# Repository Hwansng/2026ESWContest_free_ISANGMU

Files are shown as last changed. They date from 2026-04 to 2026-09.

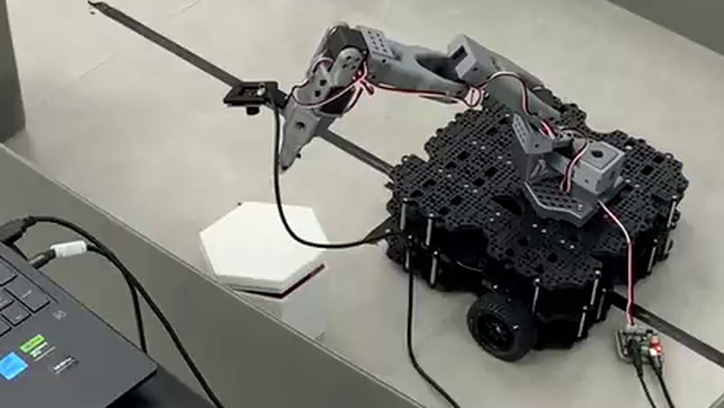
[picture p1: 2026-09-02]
report/빌드/img/grip4.png

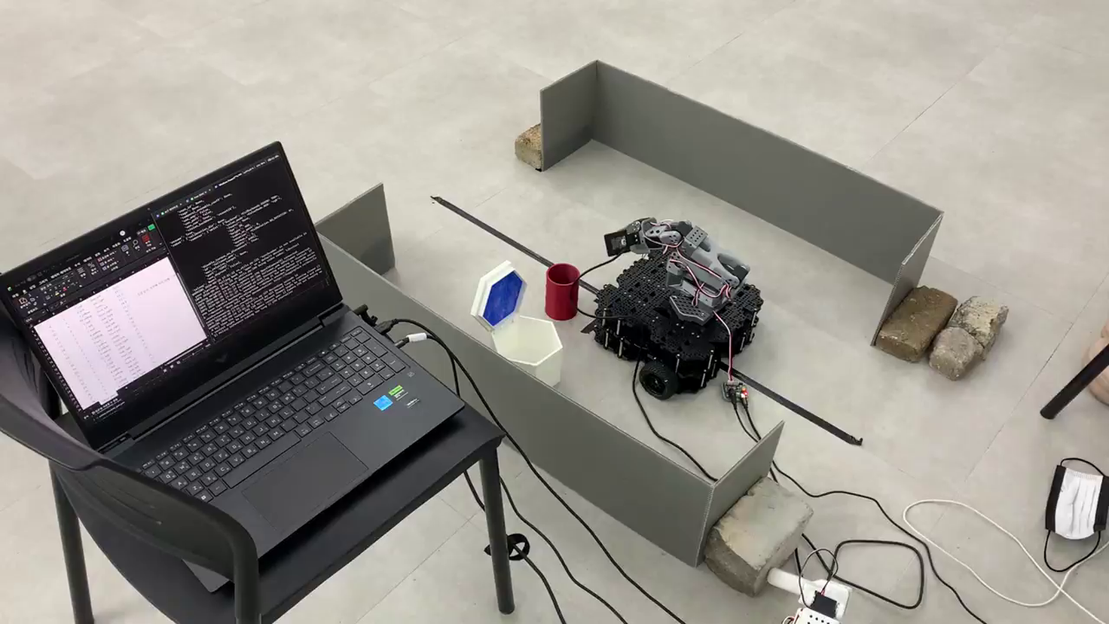
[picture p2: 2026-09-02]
report/빌드/img/rollout_wide.png

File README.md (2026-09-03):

# 🤖 HazardBot — 자율 위험물 탐지·격리 로봇 시스템

# ➕ 참가정보
 - 2026년 임베디드 소프트웨어 경진대회 (자유공모 부문)
 - 팀명: 이상무
 - 작품명: HazardBot — STS3215 직렬 버스 서보 기반 6DOF 적응형 파지 미션 기반 자율 위험물 탐지·격리 로봇 시스템
 - 팀원: 박승환, 윤강희, 이진우
 <br>

 - 주제: 듀얼 ESP32 + Raspberry Pi 5 (8GB) + ROS2 Jazzy 기반 2계층 아키텍처를 활용한 자율 위험물 탐지·격리 로봇 제작
 - 개요: 자율주행차(AMR)가 지정 영역을 자율 순찰하며, 라즈베리파이 카메라의 엣지 AI(OpenCV HSV + minAreaRect 방위각 분류)와 5종 환경 센서의 퓨전 알고리즘으로 위험물을 탐지·분류한다. 위험 등급 판별 후, UART 직렬 버스로 제어되는 6축(6DOF) Feetech STS3215 로봇 암(SO-ARM101 프레임 3D 프린팅 자체 제작)이 비대칭 물체의 방위각을 인식하고 실시간 부하(Load) 센싱 기반 컴플라이언스 토크 제어로 적응형 파지·운반 후 격리 구역의 색상별 격리함에 안전하게 배치하는 완전 자동화 미션 수행 시스템을 구현한다.
 - 개발 목표:
      - 듀얼 ESP32 기반 Fault Isolation 아키텍처 구축
      - Feetech STS3215 직렬 버스 6축 서보 데이지 체인 제어
      - 실시간 Load 센싱 기반 컴플라이언스 토크 제어 (적응형 파지)
      - OpenCV HSV + minAreaRect 방위각 분류 (60fps 엣지 비전)
      - MQ-2 가스 센서 3초 게이트 판정 (5ms × 600 표본) + 화염·거리·라인 센서 퓨전
      - ROS2 Jazzy 노드 통합 + Flask 실시간 관제 대시보드

 - 미션 시나리오:
   ```
   IDLE → PATROL → DETECTED → CLASSIFY → APPROACH → GRIP → TRANSPORT → ISOLATE → REPORT
   ```

 - 개발영상: https://youtu.be/ElTdSD-DXlM (2분 38초 · 1080p)

 ---
 # ➕ Needed (architecture)

 | `Device` | `OS` | `Middleware` | `Else` |
 | --- | --- | --- | --- |
 | Raspberry Pi 5 (8GB) | Ubuntu 24.04 LTS | ROS2 Jazzy | OpenCV 4.x, Flask + WebSocket, rosbag |
 | ESP32 DevKit V1 — **DRIVE** | Arduino-ESP32 3.0 | FreeRTOS (듀얼 코어) | TB6612FNG, VL53L1X, 5ch IR |
 | ESP32 DevKit V1 — **ENV** | Arduino-ESP32 3.0 | FreeRTOS (듀얼 코어) | MQ-2, KY-026, NeoPixel, Buzzer |
 | 학습·제어 PC (Windows 11) | — | LeRobot 0.4.4 | Feetech STS3215 × 12 (USB 반이중 어댑터), ACT |

 다음과 같은 개발환경에서 본 프로젝트를 진행한다. 모든 RPi 5 ↔ ESP32 통신은 Wi-Fi TCP 듀얼 채널이며, `<CMD,VALUE,...,CS>\n` 포맷에 **ASCII 합 % 256** 체크섬(10진수)을 사용한다.

 > **설계 변경 이력.** 초기 구상은 ESP32 한 대가 STS3215 를 UART2 로 직접 구동하는 것이었으나,
 > STS3215 는 **1선 반이중** 버스라 마스터가 하나여야 한다. ESP32 를 서보 3핀 버스에 물리면
 > 충돌이 난다. 현재는 **USB 반이중 어댑터 하나**를 마스터로 두고 PC 의 LeRobot 이 양팔을 제어한다.
 > 보드 호칭도 `#1`·`#2` 번호가 문서마다 반대를 가리켜 **DRIVE / ENV** 로 통일했다.
 > 근거와 절차는 [`docs/06_firmware/센서_지도.md`](docs/06_firmware/센서_지도.md) 와
 > [`docs/05_arm/로봇암_구축기록.md`](docs/05_arm/로봇암_구축기록.md) 참조.

 ---
 # ➕ Hardware

 | 분류 | 부품 | 용도 |
 | --- | --- | --- |
 | MCU — DRIVE | ESP32 DevKit V1 | DC 모터 · 라인트레이싱 · VL53L1X · **모터 정지 단독 권한** |
 | MCU — ENV | ESP32 DevKit V1 | 가스·화염 환경 감시 · NeoPixel · 부저 |
 | SBC | Raspberry Pi 5 (8GB) | ROS2 Jazzy + OpenCV + 대시보드 |
 | 모터 드라이버 | TB6612FNG | DC 모터 (MOSFET, 효율 95%+) |
 | DC 모터 | JGA25-371 12V | 2WD 차동 구동 (334rpm) |
 | 서보 | Feetech STS3215 × 12 | 리더·팔로워 양팔 6DOF. 1선 반이중 버스, 마스터는 USB 어댑터 하나 (12-bit, 30kg·cm) |
 | 거리 센서 | VL53L1X (ToF) | 정면 장애물 **로컬 정지 반사**(300mm · 3회 연속) · APPROACH 트리거 |
 | 가스 센서 | MQ-2 | 3초 게이트 판정 — MQ-135 는 미채택(`docs/06_firmware/센서_지도.md` §2) |
 | ~~온도 센서~~ | ~~MLX90614~~ | **미채택** — 근거는 `docs/06_firmware/센서_지도.md` |
 | 화염 센서 | KY-026 | 화염 감지 (즉시 정지) |
 | 라인 센서 | 5채널 IR 라인센서 | 라인트레이싱 PID + 이탈 감지 |
 | 프레임 | SO-ARM101 (3D 출력) | LeRobot 오픈소스 STL 자체 제작 |
 | 카메라 | RPi Camera v2 | OpenCV HSV + minAreaRect (60fps) |
 | 전원 | 3S LiPo 11.1V | **XL4016** → RPi 5 전용 · **XL4015** → 1to2 XT60 → ESP32 2보드. 실배선 정본은 [`docs/06_firmware/전력계통_실배선_2026-08-28.md`](docs/06_firmware/전력계통_실배선_2026-08-28.md) |

 ---
 # ➕ System Process

 다양한 보드와 개발환경을 함께 사용하므로, 코드를 한 번에 실행하지 않고 보드별로 분리하여 실행한다. 그에 따라 실행 순서를 정리해두었다.

 <details>
 <summary>✏️ 실행 명령어 (요약)</summary>

```
1. Wi-Fi 라우터 부팅 + 양쪽 ESP32 시리얼 포트(COMx) 확인

2. DRIVE 보드 펌웨어 업로드:
   Arduino IDE → firmware/esp32_drive/esp32_line_pid/esp32_line_pid.ino 열기
   Tools → Board: "ESP32 Dev Module" → Port 선택 → Upload

3. ENV 보드 펌웨어 업로드:
   먼저 firmware/esp32_env/libraries/AMRDemoScenarioLogic/ 를 Arduino/libraries/ 에 복사
   그리고 wifi_secrets.example.h 를 wifi_secrets.h 로 복사해 SSID/비밀번호를 채운다
   Arduino IDE → firmware/esp32_env/AMR_state_v11_ino/AMR_state_v11_ino.ino 열기
   Tools → Board: "ESP32 Dev Module" → Port 선택 → Upload
   ※ 자세한 절차는 firmware/esp32_env/README.md

   ※ 로봇암은 ESP32 가 아니라 PC 에서 제어한다 (1선 반이중, 마스터 하나):
      conda activate lerobot
      powershell arm/scripts/teleop.ps1 -LeaderPort COMx -FollowerPort COMy

4. RPi 5에서 ROS2 워크스페이스 빌드 및 실행:
   cd ros2_ws
   colcon build --symlink-install
   source install/setup.bash
   ros2 launch hazardbot_dashboard hazardbot.launch.py

5. 관제 대시보드 접속:
   브라우저에서 http://<RPi5_IP>:8080 접속
```
 </details>

 ---
 # ➕ Source code

 ## 📝 DRIVE Firmware
 스케치: [`firmware/esp32_drive/`](firmware/esp32_drive/) · 배선·확정값 정본: [`docs/06_firmware/README.md`](docs/06_firmware/README.md)
 <br>

 `라인 추종 PD · 전압 피드포워드 · ToF 논블로킹 · 모터 정지 단독 권한`

  <details>
  <summary>알고리즘 설명 (요약)</summary>

```
① 라인 추종 PD 루프 — 5채널 TCRT5000(검정 = HIGH), KP=60 · KD=25 · 주기 20ms.

② 전압 피드포워드 — 실제듀티 = 목표듀티 × (12.0 / 측정전압).
   배터리 전압이 내려가도 같은 속도를 낸다. 엔코더 속도 루프를 대체한 방식이다.

③ VL53L1X 는 논블로킹으로 읽는다. 블로킹으로 읽으면 라인 PID 주기(20ms)가 무너진다.
   정지 판정 임계는 300mm 단일 고정이다 (구간별 전환 · 마커 기반 전환은 폐기).

④ 후진은 개루프 직선이다. 라인센서가 전방에 있어 이 하드웨어로 후진 라인 추종은
   제어적으로 불가능하다.

⑤ 정지 권한 — 모터를 멈추는 것은 DRIVE 뿐이다. RPi·ENV 는 정지를 요청할 뿐 직접 끊지 않는다.
   STBY 10kΩ 풀다운으로 ESP32 가 죽거나 리셋되면 G4 가 하이임피던스가 되어 모터가 자동 정지한다.

⑥ 하트비트 — 정지는 STOP 명령이 아니라 생존 신호로 건다.
   RPi 사망 · WiFi 두절 · ENV 사망을 하나의 메커니즘으로 잡기 위해서다.

⑦ Message Format: <CMD,VALUE,CS>  예) <BUZZ,1>  — CS 를 뺀 payload 의 ASCII 합 % 256 (10진수)
```
  </details>

 ## 📝 ARM 제어 (PC · LeRobot) — 컴플라이언스 파지
 도구: [`arm/tools/`](arm/tools/) · 실행기: [`arm/scripts/teleop.ps1`](arm/scripts/teleop.ps1)
 <br>

 `STS3215 양팔 12축 반이중 버스 제어 · 실시간 Load 센싱 · 적응형 파지`

  <details>
  <summary>알고리즘 설명 (요약)</summary>

```
① USB 반이중 어댑터 하나를 마스터로 두고 Feetech STS3215 를 제어한다.
   STS3215 는 1선 반이중이라 마스터가 둘일 수 없다 — ESP32 를 서보 3핀 버스에 연결하지 않는다.
   12-bit 마그네틱 엔코더로 0.088° 절대 위치 피드백을 받는다.

② 리더·팔로워 텔레옵 (LeRobot 0.4.4 · Windows 11):
   - 팔로워 6축은 12V 직결. 리더 7.4V 레일은 ACT 수집·학습을 마친 뒤 삭제했다 (시연에 리더암 미사용)
   - 60초 연속 구동 오류·경고 0건 · 30ms 초과 0회 · 평균 55.5Hz (관문 G2 Exit 충족)
   - 정렬 확인을 선행하고, 실패하면 텔레옵을 시작하지 않는다

③ Compliance Grip: 실시간으로 그리퍼 서보의 Load 값을 모니터링한다.
   - 소프트 한계 (Load 40%): 재시도. 그리퍼 위치 +5mm offset 후 재폐쇄.
   - 하드 한계 (Load 80%): 즉시 토크 OFF + RPi 5에 GRIP_FAIL_HARD 보고.
   - 최대 3회 재시도 후 실패 시 SKIP → PATROL.

④ Servo Feedback Cycle: 6축을 라운드 로빈으로 매 10ms마다 1축씩 위치/부하/온도를 읽어 RPi 5로 퍼블리시한다. 평균 60Hz 텔레메트리.

⑤ Fault Isolation — 4계층 정지 체계. 모터를 멈추는 것은 DRIVE 뿐이다.
   하드웨어 풀다운(STBY 10kΩ) / DRIVE 로컬 / RPi / 사람 순으로 겹쳐 둔다.
   정지는 STOP 명령이 아니라 하트비트(생존 신호)로 건다 —
   RPi 사망 · WiFi 두절 · ENV 사망을 하나의 메커니즘으로 잡기 위해서다.
```
  </details>

 ## 📝 Vision Pipeline (RPi 5)
 위치: [`ros2_ws/src/vision_node/`](ros2_ws/src/vision_node/)
 <br>

 `OpenCV HSV + minAreaRect 방위각 분류 (60fps)`

  <details>
  <summary>알고리즘 설명 (요약)</summary>

```
① RPi Camera v2를 60fps 모드로 열어 BGR 프레임을 수신한다.

② VL53L1X ToF 센서가 위험물 근접 거리를 감지하면 vision_node에 트리거를 보낸다.

③ HSV 색공간 변환 후 격리 색상별 마스크를 생성한다 (적/청/녹 3구역).

④ Morphology(open/close)로 노이즈를 제거하고 cv2.findContours로 외곽선을 추출한다.

⑤ minAreaRect로 회전 사각형을 피팅하여 (cx, cy, width, height, angle)을 얻는다. 이 angle이 비대칭 물체의 방위각이며 6축 IK의 손목 회전 명령으로 매핑된다.

⑥ 결과를 /vision/detected 토픽으로 퍼블리시: {color, angle, depth_mm, confidence}.

⑦ Cortex-A76 2.4GHz 쿼드코어 + 8GB LPDDR4X로 60fps 처리에 여유가 있어 고속 주행 중에도 방위각 정밀도가 유지된다.
```
  </details>

 ---
 # ➕ 폴더 구조

```
2026ESWContest_free_ISANGMU/
├── .github/workflows/    # CI (Arduino 컴파일 · ROS2 colcon build)
├── arm/                  # 로봇암 · ACT (PC 측)
│   ├── tools/            # STS3215 제어·진단 도구 17종
│   ├── act/              # ACT 수집·검수 도구 + dataset_meta/ (100 에피소드 메타)
│   ├── calibration/      # 캘리브레이션 정본 4개 + 백업·복원 절차
│   ├── scripts/          # teleop.ps1 · record_act.ps1 · rollout_act.ps1
│   └── tests/            # ACT 수집 테스트 3종
├── docs/
│   ├── architecture.md   # 시스템 아키텍처 · 통신 · 판정 로직
│   ├── contributing.md   # 협업 가이드 (브랜치 전략 · PR 프로세스)
│   ├── 04_act/           # ACT 수집 설계 · 구현 계획 · 수집 작업기록
│   ├── 05_arm/           # 로봇암 구축기록 · 카메라 구성 · GPU 오프로드 기록
│   ├── 06_firmware/      # 핀 배정·배선 정본 · 센서 지도 · 구역 마커 · 전력 계통
│   ├── 07_ros2/          # lerobot 검증
│   └── 10_env_design/    # ENV·전력·구동부 설계 근거 (강희)
├── firmware/
│   ├── esp32_drive/      # DRIVE 주행 스케치 6종 (bringup · line · PID · OTA · TCP · motor)
│   ├── esp32_env/        # ENV 환경감시 스케치 (v11 정본 · v9 참고) + 자체 라이브러리
│   ├── sts3215/          # 서보 버스 점검 · ID 부여
│   ├── tools/            # ENV 프로토콜 파서 · keepalive (RPi 측)
│   └── tests/            # ENV 상태머신 로직 테스트 57건 (하드웨어 없이 실행)
├── hardware/             # 출력에 쓴 STL 3종 (리더암 · 팔로워암 · Waffle 플레이트)
├── ros2_ws/              # ROS2 패키지 (RPi 5)
├── report/               # 개발완료보고서 빌드 시스템 (python-pptx)
├── tools/                # rpi_check.py · ros2_ws_sync.ps1
├── archive/              # 폐기된 ESP32 ARM 펌웨어 · ENV 스케치 v1~v8 이력
└── README.md
```

> 계획·일정·시나리오·팀 인계 문서와 납땜 설명서 PDF 는 팀 내부 작업 자료라 저장소에 두지
> 않는다. 아래 문서들이 그 자료를 근거로 인용하는 곳이 있는데, 인용된 결론과 수치는
> 인용한 문서 안에 그대로 적혀 있다.

 ---
 # ➕ 협업 / 라이선스

 - 협업 가이드 (브랜치 전략 · 커밋 컨벤션 · PR 프로세스): [docs/contributing.md](docs/contributing.md)
 - 시스템 아키텍처 상세: [docs/architecture.md](docs/architecture.md)
 - 본 저장소는 제24회 임베디드SW경진대회 제출물이다. 대회 규정 제10조③ 에 따라 **공개(Public)** 로 유지한다.
 - Hugging Face LeRobot SO-ARM101 STL은 [원 저장소](https://github.com/huggingface/lerobot) 라이선스를 따른다.

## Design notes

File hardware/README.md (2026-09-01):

# 하드웨어 — 3D 출력물

| 파일 | 용도 | 크기 |
|---|---|---|
| `Leader_SO101.stl` | SO-ARM101 **리더암** 통합 모델 | 4.8 MB |
| `Follower_SO101.stl` | SO-ARM101 **팔로워암** 통합 모델 | 4.7 MB |
| `Waffle_Plate.stl` | TB3 Waffle 플레이트 (섀시 상판) | 12 MB |

## 출력 옵션

| 항목 | 값 |
|---|---|
| 재료 | PLA |
| 인필 | 20 ~ 30% |
| 레이어 두께 | 0.2 mm |
| 서보 피팅 공차 | 0.1 ~ 0.2 mm (출력 후 줄로 미세 다듬기) |
| 노즐 | 0.4 mm |

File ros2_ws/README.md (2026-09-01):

# ROS2 워크스페이스 (Raspberry Pi 5)

ROS2 Jazzy (Ubuntu 24.04 LTS) 기반 미션 통합 레이어.
라인 추종 AMR + 6축 암으로 순찰 구역 내 위험물(적색/황색)을 색상·형상으로 감지하고, TCP로 연결된 ENV 보드에서 가스 재검사를 받아 등급을 판정한 뒤 파지·격리하고, Flask/SocketIO 웹 대시보드로 실시간 상태를 관제하는 시스템. AMR 구동보드(port 5000), ARM 서보보드(port 5001), ENV 센서보드(port 8765) 세 개의 ESP32가 각각 Wi-Fi TCP로 Pi와 통신.

## 패키지 구성

| 패키지 | 역할 | 
|---|---|
| `amr_bridge` | AMR 구동 ESP32 TCP 브릿지 — 센서/가스/온도/배터리/근접 감지 수신, 구동·하트비트·복귀 명령 송신 |
| `arm_bridge` | ARM 서보 ESP32 TCP 브릿지 — 서보 피드백 수신, 명령/LED/부저/그립/비상정지 송신 |
| `arm_controller` | 암 "놓기(place)" 동작 전용 — 프리셋 포즈 테이블 기반, IK·파지는 담당하지 않음(의도적으로 범위 축소) |
| `arm_act_node` | ACT(모방학습) 정책으로 파지 수행  | 
| `sensor_bridge` | ENV 센서보드 TCP 브릿지 — 가스/화염/배터리/상태 수신, 가스 재검사(GAS_CHECK) 요청·응답 처리 | 
| `hazard_detector` | 위험물 등급 판정 FSM — 비전 색상 + 가스 재검사 + 화염 값을 종합해 위험 등급 판정 |
| `mission_orchestrator` | 최상위 미션 FSM (IDLE→PATROL→DETECTED→CLASSIFY→APPROACH→GRIP→TRANSPORT→ISOLATE/REPORT, EMERGENCY/RETURN 분기) | 
| `vision_node` | OpenCV HSV 임계값 + 컨투어 형상 분석(각도/종횡비/원형도)으로 색상·형상 판정 | 
| `hazardbot_dashboard` | Flask + SocketIO 관제 UI — 전 토픽 집계, MJPEG 영상 스트림, RPi5 헬스체크(온도/스로틀링) | 
| `hazardbot_dashboard/launch/` | 통합 launch 파일, 파라미터 | 

## 빌드

```bash
cd ros2_ws
colcon build --symlink-install
source install/setup.bash
```

## 실행

통합 launch 파일은 `hazardbot_bringup` 대신 `hazardbot_dashboard/launch/`에 있음.

```bash
# 전체 스택 (10개 노드: 카메라, amr_bridge, arm_bridge, sensor_bridge,
# hazard_detector, arm_controller, arm_act_node, mission_orchestrator,
# vision_node, dashboard_node)
ros2 launch hazardbot_dashboard hazardbot.launch.py

# 순찰 데모 전용 (암 관련 3개 노드 + mission_orchestrator 제외, 6개 노드만 실행)
# amr_bridge_node가 자체 하트비트를 보내므로 mission_orchestrator 없이도
# DRIVE 펌웨어가 타임아웃되지 않음
ros2 launch hazardbot_dashboard hazardbot_patrol_demo.launch.py
```

## 토픽 (요약)

| 토픽 | 타입 | 발행 노드 | 설명 |
|---|---|---|---|
| `/amr/cmd_vel` | geometry_msgs/Twist | (구독만, 발행처 미포함) | AMR 이동 명령 |
| `/amr/gas` | std_msgs/String | amr_bridge | AMR 측 가스 센서 값 |
| `/amr/temp` | std_msgs/String | amr_bridge | AMR 측 온도 값 |
| `/amr/battery` | std_msgs/Float32 | amr_bridge | AMR 배터리 전압 실측치 |
| `/amr/object_near` | std_msgs/Bool | amr_bridge | 근접 물체 감지 트리거 (vision_node가 구독) |
| `/amr/stop_index` | std_msgs/Int8 | amr_bridge | 정지 구역 인덱스 |
| `/amr/return_done` | std_msgs/Bool | amr_bridge | 복귀 완료 알림 |
| `/amr/start_request`, `/mission/heartbeat`, `/hazard/return_request` | Bool/String | mission_orchestrator 등 | amr_bridge가 구독, 시작/하트비트/복귀 명령 |
| `/arm/command` | std_msgs/String | arm_act_node, arm_controller | 6축 명령 (그립/놓기 통합 채널) |
| `/arm/grip_cmd`, `/arm/led_cmd`, `/arm/buzzer_cmd`, `/arm/emergency` | std_msgs/String | arm_act_node, mission_orchestrator | 그립/LED/부저/비상정지 명령 (arm_bridge가 구독) |
| `/arm/servo_feedback` | std_msgs/String | arm_bridge | STS3215 서보 위치/부하/온도 피드백 |
| `/arm/connected` | std_msgs/String | arm_bridge | ARM 보드 연결 상태 |
| `/arm/place_request` | std_msgs/String | mission_orchestrator | 놓기 요청 (arm_controller가 구독) |
| `/arm/grip_request`, `/arm/grip_retry` | std_msgs/String | mission_orchestrator | 그립 요청/재시도 (arm_act_node가 구독) |
| `/env/gas` | std_msgs/String | sensor_bridge | ENV 보드 가스 원시값 (mq135, mq2) |
| `/env/temp` | std_msgs/String | sensor_bridge | ENV 보드 온도/화염 감지 |
| `/env/battery` | std_msgs/Float32 | sensor_bridge | ENV 보드 배터리 전압 실측치 |
| `/env/state` | std_msgs/String | sensor_bridge | ENV 보드 상태/폴트 |
| `/env/gas_result` | std_msgs/String | sensor_bridge | 가스 재검사(GAS_CHECK) 결과 (hazard_detector가 구독) |
| `/vision/detected` | std_msgs/String | vision_node | 색상/형상 판정 결과 (JSON: color, angle, aspect_ratio 등) |
| `/hazard/detected` | std_msgs/String | hazard_detector | 위험물 등급 판정 결과 (JSON: level/type/detail) |
| `/hazard/gas_check_request` | std_msgs/String | hazard_detector | 가스 재검사 요청 (sensor_bridge가 구독) |
| `/mission/state` | std_msgs/String | mission_orchestrator | FSM 상태 (JSON) |
| `/mission/zone` | std_msgs/Int8 | mission_orchestrator | 현재 구역 |
| `/mission/start`, `/mission/reset` | std_msgs/String | (외부 트리거) | 미션 시작/리셋 |
| `/debug/force_grip` | std_msgs/String | (테스트 전용) | 강제 그립 트리거 |

> 전체 토픽 목록은 위 표 기준 요약이며, 각 노드 소스의 정확한 타입/필드는 코드 주석 참고.

## 문서

- `docs/lerobot_verification.md` — LeRobot(ACT 정책 도구) 격리 venv 배포 검증 기록. 
- `vision_node/DEPENDENCY_NOTES.md` — RPi5/Ubuntu 24.04/ROS2 Jazzy 환경에서 겪은 libcamera 이름 불일치, cv_bridge 패키지 누락, numpy 2.x ABI 충돌(`numpy<2` 고정으로 해결), OpenCV headless의 GUI 캘리브레이션 대체(Flask 웹 스트림) 이슈 기록.
- `firmware_reference/AMR_state_v8_wifi.ino` — 실제 펌웨어가 아닌 참조용 안내 파일. AMR ESP32(MQ135 가스 + KY-026 화염)가 `<SENS,gas,flame,battCv,stateCode,actionCode,faultCode,checksum>` 프레임을 Wi-Fi TCP(port 5000)로 `amr_bridge`에 전송한다는 프로토콜 스펙만 기록되어 있고, 실제 구현은 별도 저장소에 있음.

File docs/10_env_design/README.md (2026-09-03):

# ENV 보드 · 전력 · 구동부 설계 기록 (윤강희)

ENV 보드 펌웨어와 전력·모터 계통을 정하면서 남긴 **설계 근거** 문서다.
결론만 필요하면 정본을 보면 된다 — 여기는 "왜 그렇게 정했나"가 남아 있는 쪽이다.

| 문서 | 내용 |
| --- | --- |
| [`power_requirements.md`](power_requirements.md) | 부하별 소비전류 산정 → 레귤레이터 용량 결정 |
| [`lipo_voltage_measurement_plan.md`](lipo_voltage_measurement_plan.md) | 3S LiPo 전압 분압 측정 계획 |
| [`motor_driver_selection_guide.md`](motor_driver_selection_guide.md) | L298N 대신 TB6612FNG 를 고른 근거 |
| [`motor_encoder_wiring_plan.md`](motor_encoder_wiring_plan.md) | JGA25-371 엔코더 배선 |
| [`amr_v7_safety_flow.md`](amr_v7_safety_flow.md) | v7 안전 상태 전이 |
| [`rpi5_state_response_policy.md`](rpi5_state_response_policy.md) | RPi 가 ENV 상태코드에 어떻게 반응하는지 |
| [`rpi5_amr_v7_checklist.md`](rpi5_amr_v7_checklist.md) | RPi ↔ ENV 연동 점검 목록 |

## specs / plans

설계(spec) → 구현계획(plan) 순으로 짝지어 남긴 기록이다.

| 주제 | 설계 | 구현계획 |
| --- | --- | --- |
| 만능기판 배선 | [`specs/2026-07-28-amr-perfboard-wiring-design.md`](specs/2026-07-28-amr-perfboard-wiring-design.md) | — |
| VL53L1X 통합 | [`specs/2026-07-31-vl53l1x-code-first-design.md`](specs/2026-07-31-vl53l1x-code-first-design.md) | [`plans/2026-07-31-vl53l1x-code-first-implementation.md`](plans/2026-07-31-vl53l1x-code-first-implementation.md) |
| v9 3센서 | [`specs/2026-08-03-amr-v9-three-sensor-design.md`](specs/2026-08-03-amr-v9-three-sensor-design.md) | [`plans/2026-08-03-amr-v9-three-sensor-implementation.md`](plans/2026-08-03-amr-v9-three-sensor-implementation.md) |
| v10 VL53L1X | [`specs/2026-08-03-amr-v10-vl53l1x-design.md`](specs/2026-08-03-amr-v10-vl53l1x-design.md) | [`plans/2026-08-03-amr-v10-vl53l1x-implementation.md`](plans/2026-08-03-amr-v10-vl53l1x-implementation.md) |
| 납땜 설명서 | [`specs/2026-08-07-hazardbot-perfboard-soldering-manual-design.md`](specs/2026-08-07-hazardbot-perfboard-soldering-manual-design.md) | [`plans/2026-08-07-hazardbot-perfboard-soldering-manual-implementation.md`](plans/2026-08-07-hazardbot-perfboard-soldering-manual-implementation.md) |

> **VL53L1X(v10)는 최종 구성에서 빠졌다.** 설계·구현계획까지 갔다가 납땜 단계에서
> 접었다. 미채택 근거는 [`../06_firmware/센서_지도.md`](../06_firmware/센서_지도.md) 를,
> 실제 올라간 판본은 [`../../firmware/esp32_env/`](../../firmware/esp32_env/) 를 본다.

## 정본은 어디에

- 핀 배정·배선 확정값 → [`../06_firmware/README.md`](../06_firmware/README.md)
- 전력 계통 실배선 → [`../06_firmware/전력계통_실배선_2026-08-28.md`](../06_firmware/전력계통_실배선_2026-08-28.md)
- 납땜 설명서(완성본 PDF) — 강희 작성. 팀 내부 자료라 저장소에 두지 않는다.

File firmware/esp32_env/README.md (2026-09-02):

# ENV 보드 펌웨어 (ESP32 DevKit V1)

가스·화염 환경 감시, NeoPixel 상태 표시, 부저, RPi 5 와의 TCP 핸드셰이크를 담당하는
ESP32 스케치다. 담당은 **윤강희**.

> 2026-09-03 이전까지 이 스케치는 저장소에 없었다(`강희 로컬`). 대회 제출을 앞두고
> 실물에 올라간 판본을 그대로 옮겼다.

## 무엇을 올리면 되나

| 스케치 | 상태 | 설명 |
| --- | --- | --- |
| [`AMR_state_v11_ino/`](AMR_state_v11_ino/) | ✅ **정본 — 시연에 올라간 판본** | RPi 적응형 가스 핸드셰이크(`GAS_CHECK`) 포함 |
| [`AMR_state_v9_ino/`](AMR_state_v9_ino/) | 참고 | 3센서 구성. 배선 가이드 `firmware/docs/amr_v9_4sensor_*.md` 가 이 판본 기준이다 |
| [`../../archive/firmware_esp32_env_history/`](../../archive/firmware_esp32_env_history/) | 폐기 | v1~v8 · 센서 실험 스케치. 개발 경과 기록용 |

## 빌드 전에 해야 하는 일

### 1. 라이브러리

`AMR_state_v11_ino.ino` 는 프로젝트 자체 헤더 라이브러리 하나를 쓴다.

```
firmware/esp32_env/libraries/AMRDemoScenarioLogic/   →  Arduino/libraries/ 에 복사
```

판정 임계값·상태 지속시간 상수(`GAS_INSPECTION_DURATION_MS` 등)가 전부 이 헤더
[`AMRDemoScenarioLogic.h`](libraries/AMRDemoScenarioLogic/src/AMRDemoScenarioLogic.h) 안에 있다.
시연 시나리오의 판정 규칙을 확인하려면 여기를 보면 된다.

외부 라이브러리는 **쓰지 않는다.** v11 이 `#include` 하는 것은 ESP32 코어
(`WiFi.h` · `ESPmDNS.h` · `WiFiClient.h`)와 위 헤더가 전부다. MQ-2·KY-026 은
아날로그/디지털 핀을 직접 읽고, 부저(TMB12A05)는 GPIO26 을 HIGH 로 두는
액티브 모듈이라 라이브러리가 필요 없다. 가스 채널은 **MQ-2 하나**(GPIO34)다.

> ENV 보드에서 빠진 것: **MLX90614**(온도, 미채택 확정) · **MQ-135**(2026-09-03
> 가스 센서를 MQ-2 하나로 확정). 근거는
> [`docs/06_firmware/센서_지도.md`](../../docs/06_firmware/센서_지도.md) §2.
>
> ToF(VL53L1X)는 ENV 가 아니라 **DRIVE 보드** 소관이고 최종 구성에 들어 있다 —
> [`../esp32_drive/esp32_drive_tcp/`](../esp32_drive/esp32_drive_tcp/) 의 장애물 정지 반사.

### 2. Wi-Fi 접속 정보

`AMR_state_v11_ino.ino` 는 `#include "wifi_secrets.h"` 로 접속 정보를 읽는다.
**이 파일은 저장소에 올리지 않는다** (`.gitignore`).

```
cp AMR_state_v11_ino/wifi_secrets.example.h AMR_state_v11_ino/wifi_secrets.h
# 그리고 SSID · 비밀번호를 실제 값으로 채운다
```

RPi 5 는 AP 모드로 동작하고 ENV 보드는 mDNS(`hazardbot.local`)로 RPi 를 찾는다.
포트는 **8765** 로, DRIVE 보드의 5000 번과 다르다.

## 관련 문서

- 핀 배정·배선 정본 — [`docs/06_firmware/README.md`](../../docs/06_firmware/README.md)
- 센서 선정 근거 — [`docs/06_firmware/센서_지도.md`](../../docs/06_firmware/센서_지도.md)
- v11 가스 핸드셰이크 프로토콜 — [`docs/06_firmware/amr_v11_rpi_adaptive_gas_handoff_2026-08-29.md`](../../docs/06_firmware/amr_v11_rpi_adaptive_gas_handoff_2026-08-29.md)
- 전력 계통 실배선 — [`docs/06_firmware/전력계통_실배선_2026-08-28.md`](../../docs/06_firmware/전력계통_실배선_2026-08-28.md)

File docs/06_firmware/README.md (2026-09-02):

# ESP32 펌웨어 — 배선·설정 기준

**`DRIVE` 보드**(주행)의 배선과 확정값을 모아둔 문서. **핀을 바꾸면 여기부터 갱신할 것.**
보드는 **DOIT ESP32 DEVKIT V1** (ESP32-D0WD-V3), 포트 COM4, Arduino IDE 2.x + ESP32 코어 3.3.10.
**담당: 승환** (7/20 — AMR 주행이 강희에게서 이관됨. 환경 보드 `ENV` 는 강희).

> 🔵 **보드 호칭은 `DRIVE`/`ENV` 로 통일한다** 〔2026-08-01 확정〕.
> 번호(#1/#2)는 문서마다 반대로 쓰여 있어 쓰지 않는다 — 강희의 `amr_v9_4sensor_*` 문서가
> 말하는 「ESP32 #1 AMR」은 **이 문서의 보드가 아니라 `ENV`** 다.

## 파일

| 폴더 | 용도 | 상태 |
|---|---|---|
| `esp32_ota_test/` | 무선 업로드 경로 확보용 최소 스케치 | ✅ 검증 완료 (7/21) |
| `esp32_line_test/` | 라인센서 단독 확인 (모터 없음, USB 전원) | ✅ 극성·순서 확정 (7/22) |
| `esp32_drive_bringup/` | 모터 + 라인센서 통합 브링업 | ✅ **모터 방향·전 명령 확인 (7/22)** |
| `esp32_line_pid/` | 조향 PID — **가상 라인 모드** 내장 (센서 배선 없이 검증 가능) | ✅ **가상 모드 전 항목 검증 (7/22)** — 조향 방향·비례·후진 분기·이탈 선회. 실측 모드('v')·게인 튜닝은 섀시 후 |

---

## 1. 배선표

### 라인센서 — TCRT5000 5채널 (✅ 배선 완료)

| 모듈 | ESP32 | 보드 표기 |
|---|---|---|
| **VCC** | **3.3V** | `3V3` |
| GND | GND | `GND` |
| S1 (왼쪽) | GPIO 13 | `G13` |
| S2 | GPIO 18 | `G18` |
| S3 (중앙) | GPIO 19 | `G19` |
| S4 | GPIO 23 | `G23` |
| S5 (오른쪽) | GPIO 32 | `G32` |
| Near (선택·미연결) | GPIO 34 | `G34` |
| CLP (선택·미연결) | GPIO 35 | `G35` |

> 🔴 **VCC 를 5V 에 연결하지 말 것.** 모듈은 5V 사양이지만 출력이 5V 가 되어
> 5V 를 못 견디는 ESP32 GPIO 를 손상시킨다. TCRT5000 은 3.3V 에서 정상 동작한다.
>
> Near(IR 장애물)는 VL53L1X ToF 와 기능이 겹쳐 조달 계획상 불필요하다 (§4).
> CLP(범퍼 스위치)는 물리 충돌 백업으로 나중에 판단.

### 모터 — TB6612FNG (✅ 배선·방향 확인 2026-07-22)

- **모터 6가닥 중 빨강(+)·흰색(−)만 사용** — 모터 전원. 나머지는 엔코더로,
  파랑=엔코더 VCC(3.3V) · 검정=엔코더 GND · 노랑/초록=A/B 신호(1회전 11펄스)
- 🔵 **엔코더 미사용 확정 (2026-07-25).** 라인센서가 이미 폐루프를 닫고 있어 중복이고,
  엔코더의 주 이득(배터리 소모에 따른 속도 저하 보정)은 **배터리 전압 피드포워드**로 대체한다:
  `실제듀티 = 목표듀티 × (12.0 / 측정전압)` — 이미 계획된 G39 분압 회로만으로 구현된다.
  → 엔코더 4가닥은 **절연 후 모터에 결속**(수축튜브 + 케이블타이). 나중에 뜯어 쓸 수 있게 짧게 자르지 말 것
- 🔵 **단, 스톨 검출 슬라이스는 열어둔다 (2026-07-25).** 만능기판에 **JST-XH 3P 커넥터 `J_ENC_L`(G33 좌)·`J_ENC_R`(G36 우) 예약** (7/25 — 확장 6P 핀헤더에서 변경).
  「듀티를 주는데 200ms 동안 A상 펄스 없음 → 바퀴 걸림 → 정지·경고」— 속도 루프가 아니라 안전 진단이라
  **조향 PID 와 간섭하지 않고 튜닝 파라미터도 없다.** 채택 시 모터당 파랑(VCC **3V3**)·검정(GND)·노랑(A상) 3가닥.
  v5 의 안전 계층(팔 = Load 클램프 / 주행 = 스톨 검출)과 대칭을 이룬다
- **좌측 모터는 빨강·흰색을 교차 연결한 상태가 정방향** (7/22 확정 — 배선으로 해결, 코드 반전 없음)
- 모터 구동 중 라인센서 값 안정 확인 — 스타 그라운드 배선이 유효함
- 🔴 **캐패시터 사고 이력**: 역극성으로 장착됐던 220µF 가 VM 을 7V 로 끌어내렸다 (누설 전류
  + 브레드보드 접촉 저항). 해당 캐패시터는 폐기
- 🔵 **무캡 바닥 주행 정상 동작 확인** 〔2026-08-06 실측〕. **「캡 없이는 바닥 주행 금지」 규칙은 해제한다.**
  §3.1 의 전류 여유가 근거를 뒷받침한다 — JGA25-371 12V 권선은 **지속 스톨조차 1.0~1.2A** 로
  TB6612 연속 정격 안이다. 전원·배선 임피던스가 낮아 VM 강하가 여유 안에 들어왔다는 뜻이다.
  🔴 **단, 확인된 범위는 「모터만 물린 전원」 조건이다.** 같은 12V 레일에 **STS3215 ×6(피크 8~12A)**
  가 붙는 통합 구성은 아직 시험된 적이 없다 — 캐패시터의 세 번째 역할(공용 레일 출렁임 완충,
  v5 §3 근거 2)이 그대로 남아 있으므로 **통합 후 재확인**한다 (§3)

| TB6612 | ESP32 | 보드 표기 |
|---|---|---|
| PWMA | GPIO 25 | `G25` |
| AIN1 / AIN2 | GPIO 26 / 27 | `G26` `G27` |
| PWMB | GPIO 14 | `G14` |
| BIN1 / BIN2 | GPIO 16 / 17 | ⚠ **`RX2` / `TX2`** 로 인쇄된 보드가 많다 |
| STBY | GPIO 4 | `G4` |
| VCC (로직) | 3.3V | `3V3` |
| **GND — 로직 쪽 ×1** | GND | VCC·제어핀 줄. 로직 GND 레일로 |
| **GND — 전력 쪽 ×2** | — | VM·모터출력 줄. **12V (−) 로 직결** (벤치는 예외, 아래) |
| VM (모터) | **별도 12V** | ESP32 에서 뽑지 말 것 |
| A01/A02 | **왼쪽 모터** 빨강·흰색 (**교차 연결이 정방향**) | — |
| B01/B02 | **오른쪽 모터** 빨강·흰색 | — |

> 🔵 **GND 패드는 3개다. 3개 전부 연결한다** 〔2026-08-06 실측 확정〕.
> 7/22 에는 "2개"로 적었으나 실물은 3개였다. IC 안에 접지 네트가 셋이기 때문이다 —
> 데이터시트상 **PGND1(3·4핀)·PGND2(9·10핀)** 는 출력단 전력 접지, **GND(18핀)** 는 로직 접지.
> 보드가 이 구분을 그대로 노출하면 세 패드가 서로 안 이어져 있는 것이 정상이다.
>
> | 빠뜨린 것 | 증상 |
> |---|---|
> | 로직 GND | 제어 신호의 기준점이 없어 **방향·PWM 이 제멋대로** |
> | 전력 GND 둘 다 | 모터 전류의 귀환 경로가 없어 **모터가 안 돈다** |
> | 🔴 전력 GND 한쪽만 | **한쪽 채널만 안 돈다.** 배선을 몇 번 봐도 안 보이는 유형 — `q`/`r` 로 좌우를 따로 돌려 보면 잡힌다 |
>
> ✅ **벤치 검증 (2026-08-06)** — 3개를 전부 브레드보드 (−) 레일에 연결해 **정상 동작 확인.**
> 🔴 **단, 무부하 벤치 구성에서만 유효하다.** 바닥 주행에서는 전력 GND 2개를 굵은 선으로
> **12V (−) 터미널에 직결**해야 한다. 이유는 아래 「전원 분배」 — 브레드보드 접점 정격이
> 약 1A 인데 모터 스톨은 합산 2.4A 다. 벤치에서 되는 것이 바닥에서 되는 근거가 아니다.
>
> 어느 구성이든 두 접지가 만나는 점은 **12V (−) 한 곳뿐**이어야 한다 (스타 그라운드).
>
> **로직/전력 판별법** (모듈을 뽑고 무전원 상태에서) — ① 부저 모드로 세 패드를 서로 짚어
> 붙어 있는 것끼리 묶는다. ② 다이오드 모드로 **빨강=GND 패드 / 검정=A01** 을 대어
> **0.4~0.7V 강하가 나오면 전력 GND**(하측 FET 바디 다이오드가 PGND→출력 방향), `OL` 이면 로직이다.
> B 채널은 `B01` 로 같은 방법. PGND1 은 A01/A02 에, PGND2 는 B01/B02 에 반응한다.

- VM 입구에 **전해 캐패시터 ≥220µF/25V** — 🟡 **주행 필수 조건은 아님이 확인됨(8/6). 통합 구성 대비 권장.**
  흰 띠(−)가 GND 쪽 — 거꾸로 꽂으면 터진다
- 🔴 **13.5V 초과 금지** — 절대최대 15V, 4S 만충(16.8V)이면 즉사
- 적합성 판정은 §3.1 참조 (지속 스톨 1.2A 도 연속 정격 내)

### 전원 분배 — 브레드보드는 로직 전용

3V3 은 라인센서와 TB6612 VCC 가 함께 쓴다. TB6612 의 VCC 소비는 **1.8mA 이하**
(데이터시트 Icc, 3V 조건) 라 라인센서(약 60~90mA)에 비하면 없는 것과 같다.
모터 전류는 전부 VM→출력 경로로 흐르므로 3V3 부담과 무관하다.

### ① 벤치 구성 — ✅ 현재 상태 (2026-08-06 동작 확인)

```
ESP32 3V3 ──→ 브레드보드 (+) 레일 ──→ 라인센서 VCC · TB6612 VCC

12V (+) ─── 굵은 선 직결 ──→ TB6612 VM              🔴 브레드보드 경유 금지
12V (−) ─── 가는 선 ──→ 브레드보드 (−) 레일 ─┬─→ TB6612 GND ×3 (전력 2 + 로직 1)
                                            ├─→ ESP32 GND
                                            └─→ 라인센서 GND
TB6612 A01/A02 · B01/B02 ─── 직결 ──→ 모터          🔴 브레드보드 경유 금지
```

**GND 3개를 전부 레일에 꽂는 것으로 동작한다.** 바퀴를 띄운 무부하 시험에서는 모터 전류가
채널당 수백 mA 라 브레드보드 접점이 이를 감당한다. 방향 확인·라인센서 값 확인은 이 구성으로 끝난다.

### ② 바닥 주행 구성 — 🔴 아직 미적용 (§3)

```
ESP32 3V3 ──→ 3V3 레일 ──→ 라인센서 VCC · TB6612 VCC

12V (+) ─── 굵은 선 직결 ──→ TB6612 VM
12V (−) ─┬─ 굵은 선 직결 ──→ TB6612 전력 GND ①      ← 모터 귀환 전류
         ├─ 굵은 선 직결 ──→ TB6612 전력 GND ②      ← 데이지체인 금지, 터미널에서 만난다
         └─ 가는 선 ──→ 로직 GND 레일 ─┬─→ TB6612 로직 GND
                                       ├─→ ESP32 GND
                                       └─→ 라인센서 GND
TB6612 A01/A02 · B01/B02 ─── 직결 ──→ 모터
```

12V (−) 가 **스타 그라운드**다. 모터의 큰 전류는 굵은 선으로만 흐르고 로직 기준선에는
타지 않으므로, 모터 회전 시 라인센서 값이 흔들리는 것을 줄인다.

> 🔴 **①에서 ②로 넘어가는 것은 선택이 아니다.** 바닥에서는 마찰·경사·기동 전류가 붙어
> 스톨 합산 2.4A 까지 간다. 브레드보드 접점 정격은 약 1A 이고 접점당 접촉 저항이
> 수십~수백 mΩ 라 전압 강하로 나타난다 — **7/22 VM=7V 사건의 한 요인이 이것이었다.**

> 🔴 **12V 와 모터 출력은 브레드보드에 올리지 않는다.** 모터 전류가 스톨 시 2.4A 인데
> 브레드보드 접점 정격은 약 1A 라 발열·전압강하가 생긴다. 더 큰 이유는 안전으로,
> 12V 가 3V3 레일과 만나면 ESP32 와 라인센서가 동시에 파손된다.

### 배터리 감시 (미배선)

| | ESP32 | 보드 표기 |
|---|---|---|
| 33k/10k 분압 중점 | GPIO 39 | ⚠ **`SN`** (또는 `VN`) — EN 버튼 옆 |

전압 계수는 이론값 ×4.3 이므로 **멀티미터와 대조해 보정할 것.**

### 핀 배치 근거

- WiFi 사용 중 **ADC2 사용 불가** → 아날로그 입력은 전부 ADC1 (32~39)
- GPIO 34~39 는 **입력 전용** → 센서 입력에만 쓰고 출력 핀을 아낀다
- 스트래핑 핀 **0, 2, 5, 12, 15** 는 출력으로 쓰지 않는다 (부팅 모드 변경)
- GPIO **6~11 은 내장 플래시 전용** — 절대 사용 금지
- I2C (VL53L1X) 용으로 **GPIO 21/22 를 비워둠**

### 보드 표기 함정

| GPIO | 실크스크린 |
|---|---|
| 36 | `SP` / `VP` / `SVP` |
| 39 | `SN` / `VN` / `SVN` |
| 16 / 17 | `RX2` / `TX2` |
| 그 외 | `G13` 처럼 `G`+숫자 (`G` 하나만 = **GND**) |

---

## 2. 확정된 설정값

| 항목 | 값 | 근거 |
|---|---|---|
| 라인 감지 극성 | **검정에서 HIGH** (`LINE_ACTIVE_LOW = false`) | 2026-07-22 실측 |
| 채널 순서 | **정방향** — S1 이 로봇 기준 왼쪽 | 2026-07-22 실측 |
| 모터 방향 | `q`=좌 전진 / `r`=우 전진 / `w`=전진 — **현재 배선이 기준** (좌측은 교차 연결) | 2026-07-22 실측 |
| 모터-센서 간섭 | 모터 구동 중 라인센서 안정 (무부하·캐패시터 없이도) | 2026-07-22 실측 |
| 라인 위치 스케일 | 감지 채널의 가중 평균 **−2 ~ +2** (미감지 = 이탈) | 설계 |
| 조향 PID 구조 | 위치 → **PD** 제어 → 좌우 듀티 차 (좌=기본+보정 / 우=기본−보정). **KI 없음** — 이탈 시 적분 누적 폭주 방지 | 설계, 가상 모드 검증 (7/22) |
| PID 초깃값 | KP=60 · KD=25 · 기본속도 120 · 주기 20ms(50Hz) — **벤치 방향 검증용. 실전 값은 섀시 트랙에서 튜닝** | `esp32_line_pid` |
| 이탈 동작 | 마지막 라인 위치 방향으로 기본속도 절반 제자리 선회 | 가상 모드 검증 (7/22) |
| PWM | 20kHz / 8bit (0~255) | 가청 대역 위, TB6612 100kHz 이내 |
| WiFi | iPhone 핫스팟 `Hwan` — **호환성 최대화 ON** (2.4GHz) | ESP32 는 5GHz 불가 |
| OTA 호스트명 | `hazardbot-drive` (ESP32 #2 는 `hazardbot-env` 예정) | — |

---

## 3. 🔴 남은 설정

### 바닥 주행 전에 (섀시 무관)

- ~~**새 전해 캐패시터 장착** — 이것 없이 바닥 주행 금지~~
  → 🔵 **차단 조건에서 해제 (2026-08-06).** 캡 없이 바닥 주행이 정상 동작함을 실측 확인.
  **지금 단계에서 캐패시터는 주행의 전제가 아니다.**
  ✅ 부품은 이미 있다 (`470µF/25V`, 8/3 조달 확인) — 아래 재확인 시점에 쓴다.
  🔴 **흰 띠(−)가 GND 쪽.** 거꾸로 꽂으면 터진다 — 지난번 사고가 정확히 이것이었다
  > 별도로 **`2200µF/25V`** 도 보유 중인데 그건 **RPi 쪽 DFR0753 출력용**이다 (v5 §1 ⑦). 여기 쓰지 말 것.
- 12V·모터 배선을 브레드보드 경유에서 **직결(22AWG 이상)** 로 교체
- **전력 GND 2개를 브레드보드 레일에서 떼어 12V(−) 터미널로 직결**, 로직 GND 1개만 레일에 남긴다
  > 🔵 두 항목 모두 **주행 차단 조건이 아님이 확인됐다 (2026-08-06)** — GND 3개를 전부 브레드보드
  > 레일에 꽂은 채로 바닥 주행이 정상 동작했다. 그래도 옮기는 이유는 전류가 아니라 **진동**이다:
  > Dupont 유지력은 20회 삽입 후 1.5N → 0.5N 이하로 영구 변형되고, 3분 원테이크 중 한 번 빠지면
  > 재촬영이다 (`만능기판_이전_가이드.md` 「왜 옮기는가」). 급한 항목은 아니지만 **촬영 전에는 한다**
- 배터리 감시 분압(33k/10k → SN) 연결 + 계수(×4.3) 멀티미터 보정

### 🟡 통합 구성에서 재확인할 것 (팔·RPi 가 같은 배터리에 붙은 뒤)

지금까지의 확인은 전부 **모터만 물린 전원**에서 이뤄졌다. 아래는 그 조건이 깨질 때 다시 봐야 한다.

| 항목 | 재확인 이유 |
|---|---|
| **VM 캐패시터 470µF** | STS3215 ×6 피크 **8~12A** 가 같은 레일에서 만드는 전압 출렁임 (v5 §3 근거 2). 모터 단독 시험으로는 재현되지 않는 조건 |
| **VM 실측 (`TP_VM`)** | 팔이 움직이는 순간의 최저값을 본다. v5 는 서보 피크 시 배터리가 **9.1V** 까지 처지는 것으로 잡고 있다 |
| **ESP32 리셋 여부** | 주행 중 재부팅은 테이크 폐기다. 팔 동작과 모터 기동이 겹치는 순간이 최악 조건 |

**판단 기준** — 팔 동작 중 VM 강하나 ESP32 리셋이 관측되면 그때 캐패시터를 단다. 부품은 이미 있다.

### 섀시 장착 후에

**라인센서 감도(가변저항) 최종 조절.** 지금 벤치에서 맞춘 값은 임시다.

TCRT5000 은 바닥과의 거리가 **3~10mm** 일 때만 제대로 동작하고 15mm 를 넘으면 둔해진다.
손으로 들고 맞춘 높이와 섀시 장착 높이가 다르면 임계값이 전부 어긋난다.

| # | 조건 | 이유 |
|---|---|---|
| 1 | **섀시에 고정한 뒤** 실제 주행 높이에서 조절 | 거리가 임계값을 지배한다 |
| 2 | 센서면이 **바닥과 평행**하게 장착 | 기울면 채널별 거리가 달라진다 |
| 3 | **촬영할 조명 아래에서** 조절 | 주변 적외선 영향 (§5.9 와 같은 이유) |
| 4 | 흰 바닥에서 `raw=0` 이 되는 지점 + 여유 | 검정은 어차피 잡힌다. 흰색 오검출이 기준 |

> 로봇암에서 **카메라 장착 후 손목을 재측정해야 했던 것과 같은 구조**다.
> 순서를 어기면 두 번 일하게 된다.

---

## 4. 운영 규칙

- **모든 펌웨어에 WiFi + ArduinoOTA 블록을 유지할 것.** OTA 없는 펌웨어를 한 번이라도
  올리면 무선 경로가 끊겨 USB 를 다시 꽂아야 한다.
- OTA `onStart` 콜백에서 **반드시 모터를 정지**시킨다 (STBY LOW). 업로드 중 마지막 PWM 으로
  계속 도는 것을 막는다.
- **USB 와 VIN 에 동시에 전원을 넣지 말 것.** DevKit V1 은 두 경로가 보드 내부에서 만나
  레귤레이터가 손상될 수 있다. 브레드보드 상태에서는 USB 를 먼저 뽑는다.
  → 🔵 **만능기판에서는 5V→VIN 사이에 SS34 쇼트키를 넣어 하드웨어로 막는다** (2026-07-29,
  `만능기판_이전_가이드.md` §4.5). 다이오드 시험을 통과하면 이 규칙은 지킬 필요가 없어진다.
- 🔵 **주행 시 ESP32 전원 = XL4015 #B 의 5.0V → SS34 → VIN** (2026-06-17 확정).
  12V 를 VIN 에 직결하면 온보드 AMS1117 이 2.2W 를 태워 열보호로 떨어진다.
  벅을 거치면 배터리가 10V 까지 처져도 5V 가 유지되어 **모터 기동 전류로 ESP32 가 리셋되지 않는다**.
- 🔴 **XL4015 는 2대. 용도를 고정하고 재조정하지 않는다** (2026-07-29).
  `#A = 7.4V 리더암 전용` / `#B = 5.0V AMR 전용` — 라벨을 붙이고 트리머를 매니큐어로 잠근다.
  7.4V ↔ 5V 왕복 트리밍은 **절차 자체가 위험하다** (한 번 잊으면 서보 6개 전멸, ₩178,315).
  리더암 연결 전에는 **매번** 출력이 7.4V 인지 멀티미터로 확인할 것.
- 벤치에서 모터를 돌릴 때는 **바퀴를 띄운다.**
- 시리얼 모니터는 **USB 로만** 된다. 무선 상태에서 로그가 필요하면 텔넷 로거나
  RPi TCP 브리지(`sensor_bridge`, §4)를 쓴다.

---

## 5. 파티션

현재 `Default 4MB with spiffs` (앱 슬롯 1.25MB ×2). OTA 테스트 스케치가 962KB(73%) 였다.
슬롯을 90% 이상 채우게 되면 도구 → Partition Scheme 을 
`Minimal SPIFFS (1.9MB APP with OTA)` 로 바꾸고 **USB 로** 한 번 올릴 것
(파티션 테이블은 무선으로 못 바꾼다).

---

## 6. 트러블슈팅 — 7/21~22 실제 겪은 것

| 증상 | 원인 · 해결 |
|---|---|
| USB 업로드가 `Connecting....` 에서 멈춤 | **BOOT 버튼을 누른 채** 재시도 (DevKit V1 고질) |
| 시리얼 모니터 "Not connected" 인데 COM4 는 존재 | IDE 의 `serial-monitor` 프로세스가 포트를 점유한 채 UI 와 끊긴 것. 포트를 다른 것으로 바꿨다 되돌리거나 **IDE 재시작** |
| OTA 마지막에 `Unexpected response from device: '720'` | 전송 완료 후 ACK 파싱 문제 — **무해.** `100% Done` 이 떴으면 성공 |
| 무선 업로드가 조용히 실패 | Windows 방화벽. 핫스팟은 **공용 네트워크**로 잡히므로 허용 팝업에서 공용까지 체크 |
| IDE 에 네트워크 포트가 안 뜸 | mDNS 탐색 불안정 — IDE 재시작. 그래도 안 되면 espota 직접 호출 |
| ESP32 가 핫스팟에 재접속 안 됨 | 유휴 시 iPhone 이 핫스팟 광고를 멈춤 — **핫스팟 설정 화면을 한 번 열면** 재개. 펌웨어의 5초 재접속 루프가 대부분 흡수 |
| 전 서보/전 채널 무응답 (팔 쪽 경험) | 버스가 아니라 **전원·첫 커넥터**부터 볼 것. 뒤쪽 ID 만 죽으면 그 앞 연결부가 원인 |
| VM 전압이 12V 가 아니라 7V | ①역극성 캐패시터 누설 ②브레드보드 연선 접촉 저항 ③XL4015 **출력**(7.4V)을 잘못 가져옴 — 케이블 끝 개방 전압부터 재서 구분 |

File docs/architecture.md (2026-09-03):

# HazardBot 아키텍처 개요

> 계획 정본(`HazardBot_계획변경_및_개선안_v5`)은 팀 내부 문서라 저장소에 두지 않는다.
> 이 문서는 그 요약이며, 충돌하면 v5 와 각 영역 정본 문서가 이긴다.

## 2계층 + 제어 PC

```
        ┌──────────────────────────────────┐      ┌────────────────────────────┐
        │      Raspberry Pi 5 (8GB)        │      │   학습·제어 PC (Win 11)    │
        │      Ubuntu 24.04 + ROS2 Jazzy   │      │   LeRobot 0.4.4 · ACT      │
        │  vision_node · hazard_detector   │      │                            │
        │  mission_orchestrator            │      │   USB 반이중 어댑터 ×1     │
        │  amr_bridge · arm_bridge         │      │            │               │
        │  sensor_bridge · arm_act_node    │      │            ▼               │
        │  hazardbot_dashboard             │      │   STS3215 × 12 (양팔 6DOF) │
        └───────┬──────────────────┬───────┘      └────────────────────────────┘
         Wi-Fi  │                  │  Wi-Fi TCP :8765
          TCP   ▼                  ▼
   ┌────────────────────┐  ┌────────────────────┐
   │   ESP32 — DRIVE    │  │   ESP32 — ENV      │
   │   주행 (승환)      │  │   환경·안전 (강희) │
   │  - TB6612FNG 2WD   │  │  - MQ-2 / MQ-135   │
   │  - 5ch IR 라인추종 │  │  - KY-026 화염     │
   │  - VL53L1X ToF     │  │  - NeoPixel · 부저 │
   │  - 모터 정지 권한  │  │                    │
   └────────────────────┘  └────────────────────┘
```

**로봇암은 ESP32 가 제어하지 않는다.** STS3215 는 1선 반이중 버스라 마스터가 하나여야 한다.
ESP32 를 서보 3핀 버스에 물리면 USB 어댑터와 충돌한다. 초기 설계(ESP32 UART2 직결)는
폐기했고 코드는 [`archive/firmware_esp32_arm/`](../archive/firmware_esp32_arm/) 에 남겨 뒀다.

**보드 번호(`#1`·`#2`)는 쓰지 않는다.** 문서마다 반대를 가리켜 사고가 난 뒤 폐지하고
**DRIVE / ENV** 로 통일했다.

## 감지 3계층

판단 기준은 「누가 이 데이터로 행동하는가」다. 정본은
[`firmware/docs/센서_지도.md`](06_firmware/센서_지도.md).

| 계층 | 주기 | 센서 | 행동 주체 |
|---|---|---|---|
| 실시간 반사 | 20ms | 5ch IR 라인센서 · VL53L1X | DRIVE 단독 |
| 환경 감시 | 100ms | MQ-2 · MQ-135 · KY-026 | ENV → RPi |
| 인지 · 학습 | 30fps | RPi Camera · 손목 카메라 | RPi · ACT |

MLX90614(온도)는 **미채택**이다. 근거는 센서 지도 §5.

## 4계층 정지 체계

**모터를 멈추는 것은 DRIVE 뿐이다.** 나머지는 정지를 *요청*할 뿐 직접 끊지 않는다.

| 계층 | 수단 |
|---|---|
| 하드웨어 | STBY 10kΩ 풀다운 — ESP32 사망·리셋 시 G4 하이임피던스 → 모터 자동 정지 |
| DRIVE 로컬 | 하트비트 소실 · ToF 임계(300mm) · 라인 이탈 |
| RPi | 판정 결과에 따른 정지 요청 |
| 사람 | XT60 수동 차단 |

정지는 **STOP 명령이 아니라 하트비트(생존 신호)로** 건다. RPi 사망 · WiFi 두절 · ENV 사망을
하나의 메커니즘으로 잡기 위해서다. `RETURN`(복귀형)과 `EMERGENCY`(정지형)는
**하트비트 처리가 서로 반대**다.

## FSM 미션 흐름

```
IDLE → PATROL → DETECTED → CLASSIFY → APPROACH → GRIP → TRANSPORT → ISOLATE → REPORT
                                          │
                    GRIP 실패: RETRY ×3 → SKIP → PATROL
                    화염 감지: EMERGENCY (부저 + 후진 이탈, 이중 경로)
```

**판정은 구역을 모른다.** 위치가 아니라 내용으로 결정한다 — 적색 + 가스 = 위험,
적색만 = 통과, 황색 = 가스와 무관하게 항상 위험.
시나리오 정본(`시나리오_확정_2026-08-15`)은 팀 내부 문서라 저장소에 두지 않는다.

## 통신 프로토콜

`<CMD,VALUE,...,CS>\n` — XOR 8-bit 체크섬, 16진수 2자리. 예: `<BUZZ,1>`

| 항목 | 값 |
|---|---|
| ENV ↔ RPi 포트 | **8765** |
| 정지점 순번 | **모듈로 4** |
| EMERGENCY 화염 | 즉시 정지, **이중 경로** |
| `RPI_TIMEOUT` | 조정 방침은 회신 문서 참조 |

확정 경위와 12건 합의 내용은
팀 내부 인계 문서(`회신_진우_2026-08-25`)에 있다 — 저장소에는 두지 않는다.

## 항법

라인 추종(5ch IR + PD, KP=60 · KD=25 · 20ms) + **전폭 가로선 마커**(폭 40mm) +
VL53L1X 정면 감지(임계 **300mm 단일 고정**).

측면 마커는 조향을 깨뜨리고, 전폭 가로선은 좌우 오차가 자기중화된다. RFID 는 미채택이다.
정지는 **2단 정지 상태기계**로 처리하고 오검출은 4중으로 막는다. 근거는
[`firmware/docs/구역_마커_설계.md`](06_firmware/구역_마커_설계.md).

**ZONE 명칭은 쓰지 않는다.** 취급구역 하나 + 점검점 **P1~P4** 구성이다.
후진은 개루프 직선이다 — 이 하드웨어로 후진 라인 추종은 제어적으로 불가능하다.

> SLAM/Nav2 는 LiDAR 도입 시 검토한다. 현 시점에는 결정론적 항법 + Fault Isolation 이 우선이다.

## ACT (시각운동 정책)

입력은 **손목 카메라 1뷰**, 정책 **1개**로 적색·황색을 모두 처리한다. VGR 과는 직렬로 잇는다.
**학습 카메라 = 추론 카메라** 원칙을 지킨다 (도메인 갭 방지). CSI 는 ACT 에 통합하지 않는다.
설계 정본은 [`docs/act/`](04_act/) 와
[`docs/schedule/ACT_수집학습_통합계획_2026-08-25.md`](04_act/ACT_수집학습_통합계획_2026-08-25.md).

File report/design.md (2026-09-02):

# HazardBot Deck — Design System

> **Scope.** This file is the single source of truth for building the *HazardBot 개발완료보고서* slide deck. It defines the canvas, the fixed slide frame, type, color, the brand mark, and the density rules. Slide **content** lives in `PPT_구성안_2026-09-01.md`; this file says nothing about what goes on each page, only how it must look.

## 0. How to Use This File

1. Every slide is a **1280 × 720 artboard**. Nothing else. See §2.
2. The header block (chapter rail → title → subtitle → rule) sits at **identical pixel coordinates on every slide**. See §3. This is the hardest rule in the system.
3. **Pretendard is the only font.** No fallback face, no monospace, no display face, no Google Font. See §4.
4. The **HazardBot mark** (§6) is the only logo that may appear anywhere in the deck.
5. Fill the body region. A slide whose lower third is empty is a defect, not a style. See §8.
6. Reference tokens (`{colors.primary}`, `{typography.title}`, `{component.metric-strip}`) — never inline a hex or a raw px size that isn't in a table here.
7. If content does not fit the body region: split into two slides, or cut. Never shrink type below the minimums in §4, never reduce the §3 margins, never let the body scroll or overflow.

## 1. Overview

The deck is a **quiet engineering report**: an off-white parchment ground, near-black ink, hairline rules, one quiet blue, and no decorative chrome. Nothing on a slide exists to look like something — every mark on the page is either content, a label for content, or a hairline that separates two pieces of content.

The visual model is a **technical field notebook, not a marketing deck**. Slides are dense and evenly filled, the way a spec sheet is dense: a header block that never moves, a body divided into a small number of rectangular fields, and a footer that quietly states where you are. Emphasis is created by *surface change* (parchment → white field → dark tile) and by *the single accent*, never by shadows, gradients, glows, or oversized type.

**One color carries meaning, and it carries it the same way on every slide.** `{colors.primary}` (Action Blue) marks the one thing a slide is about — the key figure, the active step in a pipeline, the row that matters. Everything else is neutral: ink, muted ink, parchment, white, hairline. There is no second brand color, and no structural hue for diagrams — diagrams are monochrome and the blue marks the live element. If a slide has three colored things on it, two of them are wrong.

The one exception is the status triad (hazard / oxidizer / clear), which is *content*, not styling: it encodes 판정 결과 and appears only inside badges, chart series, and legend rows.

**Key Characteristics**

- Fixed 16:9 artboard, fixed header frame, fixed footer — the eye never re-hunts for the title.
- Parchment ground (`{colors.canvas-parchment}` #f5f5f7) with white (`{colors.canvas}`) reserved for *fields* — diagrams, screenshots, tables — so content reads as inset into the page.
- A single blue accent (`{colors.primary}` — #0066cc) carries every emphasis. No second brand color exists.
- Pretendard across the entire deck, four weights only (300 / 400 / 600 / 700).
- Hairlines instead of borders-with-weight; surface change instead of shadows. Exactly one shadow exists in the system, and it is only for photographs (§9).
- Bodies are **filled**, not centered-in-void: every slide bottom lands on a metric strip, an evidence rail, or the last row of a grid.
- Near-black tile (`{colors.surface-tile-1}` #272729) is reserved for section dividers, as rhythm at a chapter boundary — never as decoration, and never for the cover. A deck with no dividers therefore carries no dark surface at all: parchment from the first page to the last.

## 2. Canvas & Format

### 16:9, and only 16:9

| Property | Value |
|---|---|
| Artboard | **1280 × 720 px**, every slide, no exceptions |
| Aspect ratio | 16:9 — no 4:3, no A4, no portrait, no auto-height, no scrolling page |
| Export | PNG or PDF at **2×** (2560 × 1440); 3× if the deck will be projected above 1440p |
| Overflow | Forbidden. `overflow: hidden` on the slide box is a safety net, not a layout strategy |
| Bleed | None. All content sits inside the §3 safe margins |

```css
.slide {
  position: relative;
  width: 1280px;
  height: 720px;
  overflow: hidden;
  background: var(--canvas-parchment);
  color: var(--ink);
  font-family: 'Pretendard', sans-serif;
  page-break-after: always;   /* one slide per printed page */
}
@page { size: 1280px 720px; margin: 0; }
```

Slides stack vertically in the source document with a 32px gap between them for authoring convenience; that gap is a preview affordance and must not print.

### Why the fixed pixel canvas

Everything in this file is specified in absolute px against 1280 × 720. There is **no responsive behavior, no breakpoints, no fluid type**. A slide that reflows is a slide whose title moved — which §3 forbids. Scale the whole artboard with a `transform: scale()` on a wrapper if you need to preview it smaller; never scale the contents individually.

## 3. The Master Frame — Fixed Positions

Every slide carries the same four header elements at the same coordinates, and the same footer. A reader's eye should be able to rest at one height and read the title of every slide in the deck without moving.

```
 x=0                                                                    x=1280
 ┌───────────────────────────────────────────────────────────────────────┐ y=0
 │                                                                       │
 │   ◾ 03 · 시스템 구성                                          y=44 ──┼── header rail (18h)
 │                                                                       │
 │   소프트웨어 아키텍처                                          y=72 ──┼── title (44h)
 │   ROS2 노드·토픽 그래프                                       y=122 ──┼── subtitle (24h)
 │   ─────────────────────────────────────────────────────────  y=158 ──┼── rule (1px)
 │                                                                       │
 │   ┌─────────────────────────────────────────────────────────┐ y=176 ─┼── body top
 │   │                                                         │        │
 │   │                     BODY  1152 × 488                    │        │
 │   │                                                         │        │
 │   └─────────────────────────────────────────────────────────┘ y=664 ─┼── body bottom
 │                                                                       │
 │   ▣ HazardBot 개발완료보고서                            07 / 20  y=676┼── footer (20h)
 └───────────────────────────────────────────────────────────────────────┘ y=720
 x=64                                                             x=1216
```

### Coordinate table — memorize this

| Token | Region | x | y | width | height |
|---|---|---|---|---|---|
| `{frame.slide}` | Artboard | 0 | 0 | 1280 | 720 |
| `{frame.rail}` | Chapter rail | 64 | 44 | 1152 | 18 |
| `{frame.title}` | Slide title | 64 | 72 | 1152 | 44 |
| `{frame.subtitle}` | Slide subtitle | 64 | 122 | 1152 | 24 |
| `{frame.rule}` | Header hairline | 64 | 158 | 1152 | 1 |
| `{frame.body}` | Body region | 64 | 176 | 1152 | 488 |
| `{frame.footer}` | Footer bar | 64 | 676 | 1152 | 20 |

Safe margins: **64 left · 64 right · 44 top · 24 bottom**. Content never crosses them.

```css
.rail     { position:absolute; left:64px; top:44px;  width:1152px; height:18px;  }
.title    { position:absolute; left:64px; top:72px;  width:1152px; height:44px;  }
.subtitle { position:absolute; left:64px; top:122px; width:1152px; height:24px;  }
.rule     { position:absolute; left:64px; top:158px; width:1152px; height:1px;
            background: var(--hairline); }
.body     { position:absolute; left:64px; top:176px; width:1152px; height:488px; }
.footer   { position:absolute; left:64px; top:676px; width:1152px; height:20px;
            display:flex; align-items:center; justify-content:space-between; }
```

### Rules that make the frame hold

- **Title is always one line.** 36px SemiBold in 1152px fits roughly 34 Korean characters. If it doesn't fit, rewrite the title — do not wrap it, do not shrink it, do not let it push the subtitle down.
- **Subtitle height is reserved whether or not it is used.** A slide with no subtitle leaves the 24px band empty; the rule stays at y=158. Never close the gap.
- **The rail is never empty.** Format: `{chapter number, 2 digits} · {chapter name}`, preceded by a 6×6px amber square at 6px gap. Same chapter name for every slide in that chapter.
- **The footer is never empty and never changes shape.** Left: the 18px mark + `HazardBot 개발완료보고서`. Right: `{page, 2 digits} / 20`. Nothing else ever goes in the footer.
- **The three exceptions, and only these three:**
  1. `{component.slide-cover}` — parchment ground like every other slide, but no rail, no rule, no footer, no page number.
  2. `{component.slide-divider}` — dark ground, but the rail / title / subtitle / rule / footer stay at the *exact same coordinates*; only the surface and ink colors invert.
  3. `{component.slide-full-bleed}` — a single edge-to-edge photograph or dashboard capture. The header block still sits at its coordinates, over a scrim (§9). The body region is what goes full-bleed, not the frame.

## 4. Typography — Pretendard Only

### Font family

**Pretendard is the only typeface in this deck.** There is no display face, no secondary UI face, no monospace face, and no system fallback that is expected to ever render. Big Shoulders — used for the wordmark in the original mark artifact — is **not used here**; the HazardBot wordmark is reset in Pretendard Bold (§6).

```css
@font-face { font-family:'Pretendard'; font-weight:300;
             src:url('./폰트/Pretendard-Light.otf')    format('opentype'); font-display:block; }
@font-face { font-family:'Pretendard'; font-weight:400;
             src:url('./폰트/Pretendard-Regular.otf')  format('opentype'); font-display:block; }
@font-face { font-family:'Pretendard'; font-weight:600;
             src:url('./폰트/Pretendard-SemiBold.otf') format('opentype'); font-display:block; }
@font-face { font-family:'Pretendard'; font-weight:700;
             src:url('./폰트/Pretendard-Bold.otf')     format('opentype'); font-display:block; }

:root { font-family:'Pretendard', sans-serif; }
```

**Font loading, by output path** — the deck is wrong if Pretendard fails to load, so pick the right one:

- **Local HTML → print to PDF (recommended).** Use the `url()` declarations above; the OTFs in `PPT/폰트/` load directly, size is irrelevant. If the toolchain mangles the non-ASCII folder name, copy `폰트/` to `./fonts/` and update the paths.
- **Published as an Artifact.** External stylesheets are restricted to `fonts.googleapis.com`, and Pretendard is not hosted there — a jsDelivr or CDN stylesheet **will silently fail**. Convert the four weights to `.woff2`, subset to Hangul + Latin + digits, and inline them as `data:font/woff2;base64,…` inside the `@font-face` blocks.
- Never write a fallback chain that could actually resolve (`-apple-system`, `Malgun Gothic`, `sans-serif` as a real target). A missing Pretendard must look broken, so it gets fixed.

### Weight ladder — 300 / 400 / 600 / 700

Only four weights are used. Thin, ExtraLight, Medium, ExtraBold, and Black are present in the folder but are **not part of this system** — do not reach for them to solve a hierarchy problem. Emphasis inside body copy is 600, never 500 and never 800.

### Hierarchy

| Token | Size | Weight | Line Height | Letter Spacing | Use |
|---|---|---|---|---|---|
| `{typography.deck-title}` | 60px | 700 | 1.06 | -0.025em | Cover title only |
| `{typography.deck-subtitle}` | 20px | 400 | 1.5 | -0.01em | Cover one-line summary |
| `{typography.section-numeral}` | 96px | 700 | 1.0 | -0.03em | Section divider chapter numeral |
| `{typography.rail}` | 13px | 600 | 1.0 | 0.12em | Chapter rail |
| `{typography.title}` | 36px | 600 | 1.15 | -0.02em | Slide title (one line, always) |
| `{typography.subtitle}` | 17px | 400 | 1.45 | -0.01em | Slide subtitle, `{colors.ink-muted-80}` |
| `{typography.lead}` | 22px | 300 | 1.55 | -0.01em | Single-statement slides (goal, conclusion) — rare, and the only use of weight 300 |
| `{typography.card-title}` | 19px | 600 | 1.35 | -0.015em | Card and field headings |
| `{typography.body}` | 16px | 400 | 1.65 | -0.005em | Default body copy |
| `{typography.body-strong}` | 16px | 600 | 1.65 | -0.005em | Inline emphasis inside body copy |
| `{typography.body-dense}` | 14px | 400 | 1.6 | 0 | 4-column cards, side rails, list-heavy fields |
| `{typography.label}` | 12px | 600 | 1.2 | 0.08em | Eyebrow labels inside cards and fields |
| `{typography.metric}` | 44px | 700 | 1.0 | -0.02em | Key figures — `tnum` on |
| `{typography.metric-sub}` | 15px | 600 | 1.3 | 0 | Metric caption line |
| `{typography.chip}` | 13px | 400 | 1.0 | 0 | Topic / node / file names — `tnum` on |
| `{typography.caption}` | 12px | 400 | 1.5 | 0 | Image and diagram captions |
| `{typography.footnote}` | 11px | 400 | 1.45 | 0 | Evidence rail, source notes |
| `{typography.footer}` | 11px | 600 | 1.0 | 0.06em | Footer bar, page number |

**Absolute minimum size: 11px.** At 1280×720 projected to 1080p that renders at ~16.5px — legible from the back of a room. Anything smaller does not go on a slide; it goes in the speaker notes.

### Korean typesetting rules

These are not optional — Korean set with Latin defaults looks broken at slide sizes.

```css
.body, .card, p, li { word-break: keep-all; overflow-wrap: break-word; text-wrap: pretty; }
.metric, .chip, table { font-feature-settings: "tnum" 1; }
```

- **`word-break: keep-all`** everywhere. Korean must break at word boundaries, never mid-어절.
- **Never justify.** All Korean copy is left-aligned, ragged right. `text-align: justify` on Hangul produces rivers.
- **Line length:** 30–45 Korean characters. Past that, split the field into two columns.
- **Tabular figures (`tnum`)** on every metric, table, and chip so numbers align in columns and don't jitter between slides.
- **Pretendard has no true italic.** Never use `font-style: italic` — the browser will synthesize an oblique that is visibly wrong on Hangul. Emphasis is weight 600 or `{colors.primary}`, nothing else.
- Latin words and code identifiers inside Korean sentences stay in Pretendard. Do not switch face for `mission_orchestrator` or `/hazard/detected` — use `{component.code-chip}` instead (§11).
- Do not letterspace Hangul body copy. Positive tracking is reserved for `{typography.rail}`, `{typography.label}`, and `{typography.footer}`, which are short Latin-and-number-heavy strings.

## 5. Colors

> **Source.** This is the Apple web color system documented in the previous `design.md`, retargeted from a website to a 16:9 slide deck. Interactive roles — link, CTA, focus ring — have no meaning in a printed deck, so Action Blue is repointed from "click me" to "this is the point." Three groups are **additions**, marked as such below: a status triad (the analyzed pages surfaced no status or validation states), two derived tints, and a dark-surface hairline. Everything else is the source system unchanged.

### Brand & Accent
- **Action Blue** (`{colors.primary}` — #0066cc): The single accent, and the only brand color in the system. Nothing on a slide is clickable, so Action Blue carries emphasis rather than interaction: the rail tick, `{component.metric-block}` figures, and the one active element per slide. No second brand color exists.
- **Focus Blue** (`{colors.primary-focus}` — #0071e3): A marginally brighter sibling. The source reserved it for keyboard focus rings; the deck has none, so it is repointed to the 1.5px stroke on an active diagram node — the one place a slightly hotter blue holds its edge against a tinted fill.
- **Sky Link Blue** (`{colors.primary-on-dark}` — #2997ff): The accent on dark grounds. Action Blue goes muddy against #272729 — always swap on the cover and section dividers.
- **Blue Wash** (`{colors.primary-wash}` — #ebf3fb) — *addition*: Action Blue at ~8% over white. The fill behind an active node, a highlighted table row, or a callout band. Fill only — never text, never a rule. The source defined no tinted state because its pages never needed one.

### Surface
- **Pure White** (`{colors.canvas}` — #ffffff): What content sits *in* — diagram fields, cards, screenshot mats, table bodies. White is a field color, not a page color.
- **Parchment** (`{colors.canvas-parchment}` — #f5f5f7): The default slide ground, and the fill of nodes and chips that sit inside a white field. The signature off-white — just different enough from white to separate two surfaces without a border.
- **Pearl** (`{colors.surface-pearl}` — #fafafc): A near-white band surface, lighter than parchment so a band still reads as a band against the ground. Used for `{component.metric-strip}` and `{component.evidence-rail}`.
- **Near-Black Tile 1** (`{colors.surface-tile-1}` — #272729): The dark ground. Section dividers only — the cover is parchment (§11). A deck without dividers never uses it.
- **Near-Black Tile 2** (`{colors.surface-tile-2}` — #2a2a2c): A micro-step lighter — card surface on a dark ground.
- **Near-Black Tile 3** (`{colors.surface-tile-3}` — #252527): A micro-step darker — embedded video and image frames on a dark slide.
- **Pure Black** (`{colors.surface-black}` — #000000): True void. In a deck it appears only as the mat behind a full-bleed video still and as the pupil of the §6 mark. Never a slide ground.
- **Translucent Chip Gray** (`{colors.surface-chip-translucent}` — #d2d2d7, applied at ~64% alpha as `rgba(210, 210, 215, 0.64)`): Chips and small controls laid over a photograph.

### Text
- **Near-Black Ink** (`{colors.ink}` — #1d1d1f): Every title, every body paragraph, every table figure on a light ground. Chosen instead of pure black to keep the page photographic rather than printed. The source's `{colors.body}` carries the same hex — one near-black tone for all text on light surfaces — so the deck folds the two into `{colors.ink}`.
- **Ink Muted 80** (`{colors.ink-muted-80}` — #333333): Subtitles, card body copy, secondary reads.
- **Ink Muted 48** (`{colors.ink-muted-48}` — #7a7a7a): Captions, footnotes, the page number, axis labels, and diagram arrows with their labels.
- **Body On Dark** (`{colors.body-on-dark}` — #ffffff): All text on a dark ground.
- **Body Muted** (`{colors.body-muted}` — #cccccc): Secondary copy on a dark ground, where pure white is too loud.

### Hairlines
- **Hairline** (`{colors.hairline}` — #e0e0e0): The 1px border on every field, card, node, and table — the deck's primary structural line.
- **Divider Soft** (`{colors.divider-soft}` — #f0f0f0): Dividers *inside* a card or field, where the hairline would read as a second frame.
- **Hairline On Dark** (`{colors.hairline-on-dark}` — #3a3a3c) — *addition*: the 1px line on a dark ground. The analyzed pages carried no bordered element on a dark tile.

### Status — addition, content only
The source surfaced no status or validation colors. The deck's 판정 content needs them, so they are taken from Apple's platform semantic palette using the accessible-on-white variants. They appear **only** inside status badges, chart series, and legend rows — never as a surface, never as decoration, never as a second accent.

- **Hazard** (`{colors.status-hazard}` — #d70015 / on dark #ff6961): 위험 판정, 가스 검출, failure counts.
- **Oxidizer** (`{colors.status-oxidizer}` — #b25000 / on dark #ffd426): 황색 산화성 고체 판정.
- **Clear** (`{colors.status-clear}` — #248a3d / on dark #30db5b): 정상 / 통과 / CLEAR, success counts.

### Diagrams & Charts
The source had no diagrams and therefore no diagram color. Rather than invent a second structural hue, the deck extends the source's own logic: **diagrams are monochrome, and the single blue marks the one active element.**

- Node: `{colors.canvas-parchment}` fill, 1px `{colors.hairline}` border, label in `{colors.ink}`, description in `{colors.ink-muted-80}`.
- Active node: `{colors.primary-wash}` fill, 1.5px `{colors.primary-focus}` border. One per slide.
- Arrows, connectors, and their labels: `{colors.ink-muted-48}`.
- Chart: base series `{colors.ink-muted-48}`; the one series the slide is arguing in `{colors.primary}`; axes and gridlines `{colors.hairline}`; axis labels `{colors.ink-muted-48}`. Status colors only when the series *is* a status (성공/실패, 검출/정상). No 3D, no shadows, no rounded bar caps.

### Gradients
**None.** The source defines zero gradient tokens, and the deck keeps it that way — it is the rare system with no gradient-based token at all. Depth comes from surface change and hairlines. The only permitted non-flat fill is the §9 photo scrim.

## 6. Brand Mark

### The only logo in the deck

The **HazardBot mark** is the sole logo permitted on any slide. Do **not** place a MiniMax mark, a slide-generator watermark, a template vendor badge, a "Made with…" credit, an AI-tool logo, or any stock brand mark anywhere in the deck — cover, footer, divider, or last page. If a generation tool inserts one, remove it before export.

Institutional or partner logos (school, lab, competition) are the one possible addition; if required they go on the cover only, bottom-aligned, at the same optical weight as the mark, separated by a 1px `{colors.hairline-on-dark}` vertical divider.

### The mark

Camera eye and arm face the same direction — *what it sees is what it reaches for*. The mark carries three roles:

- **Mechanism** — body, arm, elbow, wheels, beacon stem — a solid `{colors.ink}` #1d1d1f (on dark `{colors.body-on-dark}` #ffffff). One value for every structural part; the body is a filled mass, not an outline.
- **Accent** — eye, beacon, wrist, gripper — in `{colors.primary}` #0066cc (on dark `{colors.primary-on-dark}` #2997ff). The parts that actively respond to hazard, in the deck's own accent value.
- **Pupil** — `{colors.surface-black}` #000000 on both grounds, so the direction of gaze reads independently of the surface behind it.

**Every colour in the mark is a §5 token.** There is no mark-only colour, which is why the mark drops onto any slide surface unmodified. The mark's accent does not count against the one-free-emphasis rule in §13 — the footer mark is chrome, not slide content.

```html
<!-- on parchment (#f5f5f7) / white -->
<svg viewBox="0 0 100 100" role="img" aria-label="HazardBot">
  <line x1="47" y1="39" x2="47" y2="30" stroke="#1d1d1f" stroke-width="3.5" stroke-linecap="round"/>
  <circle cx="47" cy="28" r="3.4" fill="#0066cc"/>
  <path d="M 65 47 L 81 37" fill="none" stroke="#1d1d1f" stroke-width="5.5" stroke-linecap="round"/>
  <circle cx="81" cy="37" r="3.5" fill="#1d1d1f"/>
  <path d="M 81 37 L 88 51" fill="none" stroke="#1d1d1f" stroke-width="5.5" stroke-linecap="round"/>
  <circle cx="88" cy="51" r="4.2" fill="#0066cc"/>
  <path d="M 88 51 L 95 45" fill="none" stroke="#0066cc" stroke-width="4" stroke-linecap="round"/>
  <path d="M 88 51 L 94 58" fill="none" stroke="#0066cc" stroke-width="4" stroke-linecap="round"/>
  <circle cx="38" cy="74" r="6.5" fill="#1d1d1f"/>
  <circle cx="56" cy="74" r="6.5" fill="#1d1d1f"/>
  <rect x="27" y="39" width="40" height="33" rx="14" fill="#1d1d1f"
        stroke="#1d1d1f" stroke-width="2.5"/>
  <circle cx="50" cy="55" r="9" fill="#0066cc"/>
  <circle cx="53" cy="53" r="2.2" fill="#000000"/>
</svg>
```

**On dark ground (#272729):** swap `#1d1d1f → #ffffff` and `#0066cc → #2997ff`; the pupil stays `#000000`. Nothing else changes. Define both as `<symbol>` blocks once and `<use>` them.

### Wordmark

Set **`HazardBot` in Pretendard Bold 700, tracking -0.02em**, in `{colors.ink}` (or `{colors.body-on-dark}`). The mark artifact's Big Shoulders wordmark is not used in this deck — §4 admits one face only.

### Lockups & placement

| Context | Mark size | Lockup |
|---|---|---|
| Cover | 132px | Horizontal: mark + 32px gap + wordmark at 60px / 700, tagline beneath at `{typography.label}` |
| Section divider | 40px | Mark only, top-right of the body region |
| Content slide footer | 18px | Mark + 8px gap + `HazardBot 개발완료보고서` at `{typography.footer}` |
| Minimum | 16px | Below this the gripper joints collapse — never go smaller |

- **Clear space:** half the mark's width on all four sides. Nothing enters it, including the footer text baseline box.
- Never recolor outside the two approved variants, never outline it, never rotate it, never place it on a photograph without the §9 scrim, never stretch it non-uniformly, never re-draw it in a different stroke weight.

## 7. Layout & Grid

### Grid

The body region (1152 × 488) is a **12-column grid**: column 74px, gutter 24px. Span math: `width = 98n − 24`.

| Span | Width | Typical use |
|---|---|---|
| 3 | 270px | Quarter card |
| 4 | 368px | Third card · side rail |
| 6 | 564px | Half |
| 8 | 760px | Primary field (diagram, screenshot) |
| 12 | 1152px | Full-width band |

Vertical rhythm inside the body is an **8px baseline**; row gap is always 24px.

### Spacing tokens

`{spacing.xxs}` 4 · `{spacing.xs}` 8 · `{spacing.sm}` 12 · `{spacing.md}` 16 · `{spacing.lg}` 24 · `{spacing.xl}` 32 · `{spacing.xxl}` 48

- **Card inner padding:** `{spacing.lg}` (24px). Never below 16px, never above 32px.
- **Gutter and row gap:** `{spacing.lg}` (24px), everywhere, always.
- **Label → content:** `{spacing.sm}` (12px). **Card title → body:** `{spacing.md}` (16px).
- **List item spacing:** `{spacing.sm}` (12px) between items; bullets are 5×5px `{colors.primary}` squares at 8px gap, vertically centered on the first line's x-height — not round dots, not typographic bullets.

### Alignment discipline

Everything in the body region aligns to the grid's column edges. If a field's left edge does not land on a column edge (64, 162, 260, 358, 456, 554, 652, 750, 848, 946, 1044, 1142 in slide coordinates), it is misplaced. Optical centering is allowed only inside a field, never for the field itself.

## 8. Density — Fill the Body

The body region is 1152 × 488. A three-bullet slide floating in the top 120px of it, with 368px of paper below, is the single most common defect in a deck like this — and the one this section exists to prevent.

### The fill rule

> **The bottom edge of the lowest element in the body must land between y = 640 and y = 664.**

That is: fill at least ~95% of the body's height, and never overflow it. This is checkable — measure it on every slide before export.

### How to fill — in this order

1. **Stretch the rows you have.** Cards in a row are `align-items: stretch` and fill the row's full height; they do not hug their content. A 2-card row on a 488px body means two 488px-tall cards, not two 180px cards pinned to the top.
2. **Add a bottom-pinned band.** The two standard fillers, both sized to land exactly on y = 664:
   - `{component.metric-strip}` — 1152 × 96, three or four key figures with labels. Use when the slide has numbers worth restating.
   - `{component.evidence-rail}` — 1152 × 144, three or four short evidence/source items in `{typography.footnote}` on a `{colors.canvas}` band. Use when the slide has claims worth grounding (file paths, verification counts, doc references).
3. **Promote a supporting visual.** A small diagram, a status legend, a captioned thumbnail strip — content that was going to be spoken anyway.
4. **Split the field.** A wide diagram plus a side rail (`L5`) is denser and more informative than the same diagram alone.

### How *not* to fill

- Do not scale type up to consume space. The §4 table is fixed.
- Do not vertically center a short block in the body. Content starts at the body top and grows down.
- Do not add decorative shapes, oversized icons, background patterns, watermark logos, or stock imagery as filler.
- Do not stretch a diagram beyond its natural proportions to reach the bottom edge — pair it with a rail instead.
- Do not pad a list to eight items when it has four. Add a *different kind* of block, not more of the same.

### The density ceiling

Dense is not crowded. These caps hold in every case:

- At least **35% of the body area stays quiet** — ground or field background with no ink on it.
- At most **5 top-level blocks** in the body region.
- No card smaller than **200 × 96**.
- At most **7 list items** per column, at most **9 rows** per table.
- Every field keeps its full inner padding — density comes from *more content blocks*, never from tighter margins.

## 9. Elevation & Depth

| Level | Treatment | Use |
|---|---|---|
| Flat | No border, no shadow | Slide ground, section bands, dark dividers |
| Hairline | 1px `{colors.hairline}` | Fields, cards, tables, diagram canvases |
| Surface step | `{colors.canvas}` fill on `{colors.canvas-parchment}` | Cards, metric strips, evidence rails |
| Inset field | `{colors.canvas}` fill + 1px `{colors.hairline}` | Diagram canvases, screenshot mats, table bodies |
| Photo shadow | `rgba(0, 0, 0, 0.22) 3px 5px 30px 0` | Photographs and hardware shots only — the source system's one shadow, unchanged |

**Shadow philosophy.** Exactly one shadow exists, and it applies only to photographic content — hardware shots, the arm, the demo space. Never on cards, never on text, never on diagram nodes, never on the mark. Elevation in the deck comes from surface steps and hairlines.

**Photo scrim.** The one non-flat fill in the system: when the header block or the mark must sit over a photograph, lay `linear-gradient(180deg, rgba(0,0,0,0.72) 0%, rgba(0,0,0,0.12) 62%)` over the top 240px of the image. It is a legibility device, not decoration — never use it where nothing sits on top of it.

## 10. Shapes

| Token | Value | Use |
|---|---|---|
| `{rounded.none}` | 0 | Slide ground, full-bleed bands, table cells, chart bars |
| `{rounded.xs}` | 3px | Status badges, code chips, bullet squares |
| `{rounded.sm}` | 6px | Cards, fields, screenshot mats, diagram nodes |
| `{rounded.md}` | 10px | The single hero field on an `L1` slide |
| `{rounded.full}` | 50% | Step numerals in a flow, legend dots |

Two radii grammars only: **6px for anything rectangular that holds content**, **3px for small chips**. Nothing in between, and no pill shapes — pills read as buttons, and there is nothing to click in a deck.

### Imagery geometry

- Screenshots (dashboard captures) sit in a `{component.image-mat}`: white mat, 1px `{colors.hairline}`, `{rounded.sm}`, 12px inner padding, `{typography.caption}` beneath.
- Hardware photographs are cropped to 16:9 or 4:3, `{rounded.sm}`, and carry the photo shadow.
- Never crop a photograph into a circle, a hexagon, or a blob. Never apply a color overlay other than the scrim.
- Every image carries a caption in `{typography.caption}`, `{colors.ink-muted-80}`, left-aligned to the image's left edge.

## 11. Components

### Frame

**`header-rail`** — `{frame.rail}`. A 6×6px `{colors.primary}` square + 6px gap + chapter string in `{typography.rail}`, `{colors.ink-muted-80}`. On dark: `{colors.primary-on-dark}` + `{colors.body-muted}`.

**`slide-title`** — `{frame.title}`. `{typography.title}`, `{colors.ink}`. One line. On dark: `{colors.body-on-dark}`.

**`slide-subtitle`** — `{frame.subtitle}`. `{typography.subtitle}`, `{colors.ink-muted-80}`. One line, or empty with the height reserved.

**`footer-bar`** — `{frame.footer}`. Left: 18px mark + 8px gap + deck name in `{typography.footer}`, `{colors.ink-muted-48}`. Right: `07 / 20` in `{typography.footer}`, `{colors.ink-muted-48}`, `tnum`. Never anything else.

### Content blocks

**`card`** — `{colors.canvas}` fill, 1px `{colors.hairline}` border, `{rounded.sm}`, padding `{spacing.lg}`. Optional `{typography.label}` eyebrow in `{colors.ink-muted-80}`, then `{typography.card-title}`, then `{typography.body}` or `{typography.body-dense}`. Stretches to its row height.

**`card-outlined`** — `{colors.canvas}` fill, 1px `{colors.hairline}`, `{rounded.sm}`, padding `{spacing.lg}`. Use when cards sit next to a white field and the `{colors.canvas}` fill would read as a third surface.

**`card-accent`** — `{component.card}` with a 3px `{colors.primary}` bar on its left edge and `{colors.primary-wash}` fill. **One per slide, maximum** — it marks the single most important block.

**`card-numbered`** — `{component.card}` with a 28px `{rounded.full}` numeral in `{colors.ink-muted-48}` / `{colors.body-on-dark}` at the top-left, then title and body. For ordered sequences (pipeline steps, procedure stages).

**`metric-block`** — `{typography.label}` eyebrow → `{typography.metric}` figure in `{colors.primary}` (`tnum`) → `{typography.metric-sub}` label in `{colors.ink}` → optional `{typography.caption}` qualifier in `{colors.ink-muted-80}`. The qualifier line is where "근거리 100% / 원거리 66.7%" goes — a bare 86.7% with no qualifier is a misleading slide.

**`metric-strip`** — `{colors.surface-pearl}` fill, `{rounded.sm}`, padding `{spacing.lg}`, three or four `{component.metric-block}`s in equal columns separated by 1px `{colors.divider-soft}` vertical dividers. Two heights, because a 44px figure plus a label plus a qualifier line does not fit in 96px:

- **compact — 1152 × 96** (`y = 568…664`): label + figure only. The qualifier moves into the slide body. Pairs with `L7`.
- **full — 1152 × 144** (`y = 520…664`): label + figure + `{typography.metric-sub}` qualifier. Use whenever a figure needs its conditions stated beside it — which is most figures in this deck. Pairs with `L8`.

**`evidence-rail`** — 1152 × 144, `{colors.surface-pearl}` fill, `{rounded.sm}`, padding `{spacing.lg}`. A `{typography.label}` heading, then three or four items in `{typography.footnote}`, `{colors.ink-muted-80}`, separated by 1px `{colors.divider-soft}` verticals. Holds source files, verification counts, doc references. Pinned to the body bottom (`y = 520…664`).

**`diagram-field`** — `{colors.canvas}` fill, 1px `{colors.hairline}`, `{rounded.sm}`, inner padding `{spacing.xl}`. The container for every node graph, flow chart, power tree, and architecture diagram. Nodes: `{colors.canvas-parchment}` fill, 1.5px `{colors.ink-muted-48}` stroke, `{rounded.sm}`, label in `{typography.body-dense}` 600. The *active* node in the story: `{colors.primary-wash}` fill, 1.5px `{colors.primary-focus}` stroke. One per slide. Arrows: 1.5px `{colors.ink-muted-48}` with a 7px solid arrowhead; labels in `{typography.caption}`, `{colors.ink-muted-80}`.

**`flow-step`** — A horizontal sequence inside a `{component.diagram-field}`: numbered `{rounded.full}` marker, step title in `{typography.body-dense}` 600, one-line description in `{typography.caption}`. Steps connected by a 1.5px `{colors.ink-muted-48}` line with arrowheads. The decision branch (색상 판정) forks vertically with the branch condition on the line in `{typography.caption}`.

**`status-badge`** — Inline pill-free chip: `{rounded.xs}`, 4px × 10px padding, `{typography.label}`, on a 14%-tint fill of its status color with the text in the full status color. Three variants: `-hazard`, `-oxidizer`, `-clear`. Only these three exist.

**`code-chip`** — For ROS2 topics, node names, file paths, and constants (`/hazard/detected`, `arm_act_node`, `GAS_CHECK_TIMEOUT_S`). Pretendard `{typography.chip}` with `tnum`, `{colors.ink}`, `{colors.canvas}` fill, `{rounded.xs}`, 2px × 7px padding. There is no monospace font in this deck — the chip's fill and tight tracking do the work a mono face would.

**`callout`** — Full body width, `{colors.primary-wash}` fill, 3px `{colors.primary}` left bar, `{rounded.sm}`, padding `{spacing.lg}`. `{typography.body}`. For a single quoted judgment string (`황색 산화성 고체 감지 — 취급구역 내 위치 자체가 위반`) or one conclusion sentence. One per slide.

**`table-spec`** — `{colors.canvas}` body, 1px `{colors.hairline}` outer, `{rounded.sm}`. Header row: `{typography.label}`, `{colors.ink-muted-80}`, `{colors.canvas}` fill, 1px `{colors.hairline}` bottom. Data rows: `{typography.body-dense}`, 1px `{colors.divider-soft}` separators, 14px vertical / 16px horizontal cell padding. Numeric columns right-aligned with `tnum`. No zebra striping, no vertical rules.

**`image-mat`** — See §10. White mat + hairline + caption.

**`legend-row`** — Horizontal run of `{typography.caption}` items, each preceded by a 10px `{rounded.full}` swatch, 20px apart. Sits directly beneath its chart or diagram, left-aligned to it.

**`bar-row`** — The deck's only chart form. A horizontal comparison bar, used when two to four categories are compared on one scale (성공률, 구간 비중). Vertical bars are not used: category names in Korean do not fit under a 100px column without rotating type, and §4 forbids rotated Hangul.

Each row is a fixed height with three zones — name at the left (`{typography.body-dense}` 600, with the raw count beneath in `{typography.footnote}` / `{colors.ink-muted-48}`), the bar in the middle, the value right-aligned at 19px/700 `{colors.ink}` with `tnum`. The bar sits in a full-width **track** of `{colors.divider-soft}` so an incomplete bar reads as a share of the whole rather than a floating rectangle; the fill is `{colors.primary}` for the one series the slide is arguing and `{colors.ink-muted-48}` for the rest. Square caps, `{rounded.none}`, no axis, no gridlines — the track *is* the axis. A summary row may follow below a 1px `{colors.divider-soft}` rule, with its figure in `{colors.primary}`.

Status colors replace the two neutrals only when the series *is* a status (성공/실패, 검출/정상). Never more than four rows; past that the comparison belongs in a `{component.table-spec}`.

**`bullet-list`** — `{typography.body}` items, 12px apart, 5×5px `{colors.primary}` square marker at 8px gap. Sub-items indent 20px with a 5×1px `{colors.ink-muted-48}` dash marker. Two levels maximum.

### Slide types

**`slide-cover`** — Full-bleed `{colors.canvas-parchment}` — **the same ground as every content slide.** The 132px mark + wordmark lockup at x=96, vertically centered slightly above the midline; `{typography.deck-subtitle}` one-line summary beneath in `{colors.ink-muted-80}`; a 1px `{colors.hairline}` rule; then team, names, and date in `{typography.label}` / `{colors.ink-muted-48}`, matching the footer's ink on every other page. The mark and wordmark use the on-light variant (§6): `{colors.ink}` mechanism, `{colors.primary}` accent and tagline. No rail, no page number, no footer. The only slide that breaks the frame entirely.

The cover is paper, not a dark plate. A near-black title card followed by nineteen parchment slides announces a different document than the one that follows; holding one ground from the first page makes the deck read as a single report and lets the mark, not a surface change, carry the opening. The dark treatment is available as a variant if a deck ever needs a title plate — but it is not the default, and a deck must not use both.

**`slide-divider`** — `{colors.surface-tile-1}`, frame coordinates unchanged. Rail, title (the chapter name), and subtitle in their dark-ground inks. Body region: `{typography.section-numeral}` chapter numeral in `{colors.primary-on-dark}` at the left, and at the right a list of that chapter's slide titles in `{typography.body-dense}`, `{colors.body-muted}`, with their page numbers — which is also what keeps the divider's body filled. 40px mark top-right.

**`slide-agenda`** — Paper ground. Two forms, chosen by chapter count:

- **Three chapters** — `L3`: three `{component.card}`s, each a chapter with its numeral, name, and the slides it contains in `{typography.body-dense}`.
- **Four to six chapters** — `L1`: one full-body `{component.diagram-field}` holding one **chapter row** per chapter, split by 1px `{colors.divider-soft}` rules. Row: 26px/700 numeral in `{colors.ink-muted-48}` at the left, chapter name in `{typography.card-title}`, its slide titles beneath in `{typography.body-dense}` / `{colors.ink-muted-80}`, and the page range right-aligned in 13px/600 `{colors.ink-muted-48}` with `tnum`. Rows divide the field's inner height equally. Cards do not scale past three — four 270px cards cannot hold six slide titles without dropping below the §4 minimum.

**`slide-full-bleed`** — Body region only goes edge to edge (the frame stays). Photograph or dashboard capture at 1280 × 488 positioned at y=176, with the §9 scrim under the header block if the image reaches it.

## 12. Body Layout Presets

Every content slide uses one of these. All dimensions are inside the 1152 × 488 body region; gap is always 24px.

| Preset | Composition | Fits |
|---|---|---|
| `L1 · full` | 1152 × 488 | One large diagram, one full-bleed capture, one big table |
| `L2 · halves` | 564 + 564 | Two parallel ideas; before/after; text ↔ image |
| `L3 · thirds` | 368 × 3 | Three components, three phases, three roles |
| `L4 · quarters` | 270 × 4 | Four hardware units, four limitations |
| `L5 · 8+4` | 760 + 368 | Diagram (left) + notes rail (right) — the workhorse |
| `L6 · 4+8` | 368 + 760 | List (left) + diagram or capture (right) |
| `L7 · stage + strip` | 1152 × 368 over 1152 × 96 | Any visual that needs its numbers restated beneath |
| `L8 · stage + band` | 1152 × 320 over 1152 × 144 | Any claim that needs evidence beneath — band is an `{component.evidence-rail}` or a full `{component.metric-strip}` |
| `L9 · 2×2` | 564 × 232, four cells | Four paired items; a comparison matrix |
| `L10 · 2×3` | 368 × 232, six cells | Six topics, six nodes, six team responsibilities |
| `L11 · flow + detail` | 1152 × 200 flow over 1152 × 264 | A pipeline plus its per-step detail |

Suggested assignment for this deck (adjust as content settles): cover → `slide-cover`; 목차 → `slide-agenda`; 배경/목표 → `L6`, `L2`; 시스템 개요 → `L5`; 하드웨어 구성 → `L4`; 소프트웨어 아키텍처 → `L5`; 판정 로직 → `L11`; GAS_CHECK → `L11`; ACT 학습/동작 → `L6`, `L7`; 통합 파이프라인 → `L11`; 대시보드 → `L3` of `image-mat`s; 전력 계통 → `L5`; 제어 경로 → `L7`; 검증 결과 → `L7`; 영상 안내 → `L1` + `metric-strip`; 한계·계획 → `L9`; 팀 구성 → `L3`; 결론 → `L8`.

## 13. Do's and Don'ts

### Do

- Keep the rail, title, subtitle, rule, and footer at their `{frame.*}` coordinates on every single slide. This is the deck's spine.
- Set everything in Pretendard, in 300 / 400 / 600 / 700 only.
- Use `{colors.primary}` for its three specced roles and nothing else: the rail tick, the `{component.metric-block}` figures, and **one** free emphasis that marks what the slide is about (an active node, a `{component.card-accent}`, or a `{component.callout}`). One free emphasis per slide, never two.
- Use `{colors.ink-muted-48}` for every diagram, arrow, and hardware block, so mechanism reads the same way on every page.
- Fill the body to y = 640–664 using a `{component.metric-strip}` or `{component.evidence-rail}` when the primary content stops short.
- Put every diagram and screenshot inside a white field with a 1px hairline — content sits *in* a field, on paper.
- Set `word-break: keep-all` on all Korean copy and `tnum` on every figure.
- Qualify every headline number where the qualification matters (86.7% carries 30회 / 근거리 100% / 원거리 66.7%).
- Use `{component.code-chip}` for topic, node, and file names instead of reaching for a monospace face.

### Don't

- Don't move, resize, or drop the header block on any slide. A slide whose title sits at a different height than the previous one is broken, however good it looks alone.
- Don't use any font but Pretendard — not for a numeral, not for a code identifier, not for the wordmark, not as a fallback.
- Don't use `font-style: italic`; Pretendard has no italic and the synthesized oblique wrecks Hangul.
- Don't place a MiniMax logo, a generator watermark, a tool badge, or any third-party mark anywhere in the deck.
- Don't leave the lower third of the body empty, and don't fix it by enlarging type or adding decorative shapes.
- Don't introduce a second accent color; don't promote a status color to a decorative or surface role.
- Don't use gradients, glows, 3D, bevels, or drop shadows on anything but a photograph.
- Don't use white as a full-slide background — white is a field color, paper is the page.
- Don't use pill radii; there is nothing clickable on a slide.
- Don't justify Korean text, don't letterspace Hangul body copy, and don't run body lines past ~45 Korean characters.
- Don't let content overflow the body region or cross the safe margins. Split the slide instead.
- Don't use `{colors.primary}` (#0066cc) on a dark tile or `{colors.primary-on-dark}` (#2997ff) on parchment — each is the wrong value on the other surface.

## 14. Iteration Guide

1. Work one slide, or one component, at a time. Reference its token key directly (`{component.metric-strip}`, `{frame.body}`, `L5`).
2. Before touching visuals, check the frame: are rail / title / subtitle / rule / footer at their exact coordinates?
3. Then check density: where does the lowest element's bottom edge land? If it's above y = 640, apply §8 in order.
4. Then check color: setting aside the rail tick and the metric figures, how many things are accent-colored? More than one free emphasis means picking the real one.
5. Variants of a component (`-accent`, `-outlined`, `-numbered`, `-hazard`) are separate entries in §11 — don't invent an undocumented variant, add one here first.
6. There are no hover, focus, or transition states — this is a printed artifact. Never document or build them.
7. When a slide feels wrong, change the layout preset before changing the type or the color. It's almost always the preset.

## 15. Known Gaps

- **Photography direction is unspecified.** The deck's hardware shots, arm wide-shots, and demo-space images come from `사진/` and `영상/`; this system defines how they're framed (§10) but not which frames to choose.
- **Chart specifics beyond the bar row.** Single-scale comparison is settled — see `{component.bar-row}` in §11. Anything beyond it (grouped bars, distributions, time series, a real axis) has no styling yet and needs a decision recorded here first. The 5-segment proportional strip on the 시연 영상 slide is a `{component.bar-row}` track split by content, not a second chart type.
- **Appendix slides.** If the deck grows past 20 pages, the footer's `/ 20` denominator and the divider slide lists both need updating; no appendix-specific frame variant is defined.
- **Print color.** Values are specified for screen and projection. In print, `{colors.canvas-parchment}` (#f5f5f7), `{colors.surface-pearl}` (#fafafc) and `{colors.canvas}` (#ffffff) sit within three points of each other and will collapse on uncoated stock — the whole light surface system becomes one flat white. For a print run, carry the structure on `{colors.hairline}` borders alone and drop the surface steps.
- **Pretendard `.woff2` subsets** are not yet built. The Artifact path in §4 requires them; the local print path does not.

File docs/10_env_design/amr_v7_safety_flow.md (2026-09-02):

# HazardBot AMR v7 안전 흐름 문서

## 목적

이 문서는 ESP32 #1 AMR v7 펌웨어의 안전 중심 구조를 설명한다. 공모전 발표와 개발 검증에서 Sensor -> Evaluation -> Action 흐름, 상태 전환 기준, RPi 5 메시지 포맷, 테스트 방법을 빠르게 확인하는 것을 목표로 한다.

## 시스템 범위

대상은 ESP32 #1 AMR 펌웨어다. ESP32 #2 ARM, STS3215 서보, 그리퍼, 출력 장치 로직은 포함하지 않는다. ESP32 #1과 ESP32 #2는 직접 통신하지 않으며, Raspberry Pi 5가 ROS2 Jazzy 기반 중앙 제어기로 각각의 ESP32와 통신한다.

## Sensor -> Evaluation -> Action 구조

### Sensor

- MQ-135: 가스 센서 입력을 읽고 이동 평균으로 안정화한다.
- KY-026: flame 감지 입력을 읽는다. 현재 기준은 LOW active다.
- Emergency Stop: `EMERGENCY_STOP_PIN` 입력을 `INPUT_PULLUP`으로 읽고 LOW일 때 활성으로 본다.
- RPi 5 통신: Serial 입력이 들어오면 마지막 수신 시간을 갱신한다.
- RPi 5 keepalive: `<CMD,PING,CS>`처럼 checksum이 맞는 framed 메시지만 통신 정상으로 인정한다.
- LiPo 전압: 현재는 `currentBatteryVoltage = 12.0` 임시값을 사용한다.

### Evaluation

`evaluateAmrState()`가 센서값과 안전 조건을 평가한다. 우선순위는 다음과 같다.

1. Emergency Stop 활성: `STOP`
2. LiPo 전압 `9.9V` 이하: `STOP`
3. MQ-135 센서 오류: `SENSOR_ERROR`
4. RPi 5 통신 timeout: `STOP`
5. flame 감지 또는 gas danger 조건: `DANGER`
6. gas warning 조건: `WARNING`
7. 그 외: `SAFE`

### Action

현재 Action은 상태 메시지를 RPi 5로 전송하고, 상태별 AMR action을 분류하는 것이다. 상태가 바뀌면 즉시 전송하고, 상태 변화가 없어도 heartbeat 주기마다 다시 전송한다. 실제 모터 핀 제어는 아직 수행하지 않으며, `applyAmrAction()`은 나중에 모터 제어를 붙일 안전한 hook 역할만 한다.

| 상태 | Action | 의미 |
|---|---|---|
| `SAFE` | `NORMAL_MOTION` | 정상 주행 허용 |
| `WARNING` | `LIMITED_MOTION` | 제한 주행 또는 감속 대상 |
| `DANGER` | `STOP_MOTION` | 정지 대상 |
| `STOP` | `STOP_MOTION` | 정지 대상 |
| `SENSOR_ERROR` | `STOP_MOTION` | 정지 대상 |

## 상태 정의

| 상태 | 의미 | 진입 조건 |
|---|---|---|
| `SAFE` | 정상 감시 상태 | 위험 조건 없음 |
| `WARNING` | 주의 상태 | gas가 warning 진입 기준 이상 |
| `DANGER` | 위험 상태 | flame 감지 또는 gas danger 조건이 연속 기준 충족 |
| `STOP` | 즉시 정지 상태 | Emergency Stop, LiPo cutoff, RPi timeout |
| `SENSOR_ERROR` | 센서 fault 상태 | MQ-135 값이 유효 범위를 연속 이탈 |

## 주요 안전 기준

- 3S LiPo cutoff: `LIPO_CUTOFF_VOLTAGE = 9.9`
- Emergency Stop 핀: `EMERGENCY_STOP_PIN = 26`
- RPi timeout: `RPI_TIMEOUT_MS = 3000`
- Sensor error 연속 기준: `SENSOR_ERROR_COUNT_THRESHOLD = 3`
- DANGER 연속 기준: `DANGER_COUNT_THRESHOLD = 3`

## 메시지 포맷

RPi 5로 전송되는 메시지는 다음 형식을 사용한다.

```text
<CMD,STATE=상태,GAS=가스값,FLAME=0또는1,BAT=전압,CS>
```

예시:

```text
<CMD,STATE=SAFE,GAS=42,FLAME=0,BAT=12.00,56>
```

checksum은 `<`, `>`, checksum 필드를 제외한 payload 문자열을 XOR 계산한다.

```text
CMD,STATE=SAFE,GAS=42,FLAME=0,BAT=12.00
```

RPi 5가 ESP32 #1 timeout을 해제하려면 checksum이 맞는 framed 메시지를 보내야 한다. 현재 keepalive 예시는 다음과 같다.

```text
<CMD,PING,76>
```

여기서 `76`은 `CMD,PING` payload의 XOR checksum이다. checksum이 틀린 메시지는 timeout 해제에 사용하지 않는다.

RPi 5 또는 PC에서 keepalive 메시지를 확인하려면 다음 dry-run 명령을 실행한다.

```powershell
C:\Users\rkdgm\.cache\codex-runtimes\codex-primary-runtime\dependencies\python\python.exe tools\rpi_keepalive.py --dry-run --count 2
```

실제 Serial 포트로 보낼 때는 `pyserial`이 필요하며, 포트를 지정해서 실행한다.

```powershell
python tools\rpi_keepalive.py --port COM5 --interval 1
```

## 테스트 방법

하드웨어 없이 먼저 Python pure logic 하네스를 실행한다.

```powershell
C:\Users\rkdgm\.cache\codex-runtimes\codex-primary-runtime\dependencies\python\python.exe tests\amr_v7\test_amr_v7_pure.py
```

현재 하네스는 상태 문자열, 메시지 포맷, checksum, LiPo cutoff, SENSOR_ERROR, Emergency Stop, RPi timeout fallback을 확인한다.

실제 ESP32 보드에서는 다음을 추가 확인한다.

- Serial Monitor에 `<CMD,...,CS>` 메시지가 출력되는가?
- E-Stop 버튼을 누르면 즉시 `STOP`으로 전환되는가?
- RPi 5 입력이 3초 이상 없으면 `STOP`으로 전환되는가?
- RPi 5가 주기적으로 keepalive를 보내면 timeout이 해제되는가?
- MQ-135 비정상 입력이 3회 누적되면 `SENSOR_ERROR`로 전환되는가?

## 남은 개선 과제

- 실제 LiPo 전압 분배 회로와 ADC 변환 함수 구현
- RPi 5 keepalive 메시지 주기와 payload 최종 확정
- `applyAmrAction()`에 실제 모터 드라이버 제어 연결
- 실제 RPi 5 환경에 `pyserial` 설치 및 keepalive 서비스 등록
- 실제 보드 업로드 후 핀 배선과 active level 확인
- 공모전 발표용 상태 전환 다이어그램 작성

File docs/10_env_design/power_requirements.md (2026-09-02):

# HazardBot 전원 및 배터리 요구사항

## 목적

이 문서는 HazardBot AMR의 배터리 구매 전 기준을 정리한다. 현재 팀이 실제 배터리를 아직 구입하지 않은 상태이므로, LiPo 전압 측정 코드를 확정하기 전에 전원 구조와 배터리 요구사항을 먼저 정해야 한다.

## 현재 확인된 정보

현재 확인된 구동 부품은 `DC 12V 350rpm` 모터다. 모터 단자는 다음처럼 표기되어 있다.

```text
M2, V, A, B, G, M1
```

의미는 다음일 가능성이 높다.

| 표기 | 추정 역할 |
|---|---|
| `M1`, `M2` | 모터 전원 단자 |
| `V` | 엔코더 전원 + |
| `G` | 엔코더 GND |
| `A`, `B` | 엔코더 신호 |

이 정보는 배터리 정보가 아니라 모터/엔코더 정보다. 배터리 라벨은 아직 확인되지 않았다.

ICBANQ 제품 정보 기준으로 모터 정격 전류는 `1.5A`이다. 좌우 모터 2개를 사용한다면 정격 부하 기준으로 모터만 약 `3.0A`가 필요하다. 실제 출발, 회전, 장애물 접촉, 바퀴 stall 상황에서는 이보다 더 큰 순간 전류가 필요할 수 있다.

## 배터리 후보

모터가 12V 계열이므로 배터리 후보는 다음이 적절하다.

| 후보 | 장점 | 주의점 |
|---|---|---|
| 3S LiPo 11.1V | 모터 12V 계열과 잘 맞고 출력이 좋음 | 충전/보관/과방전 관리 필요 |
| 3S Li-ion pack 11.1V 또는 12V | BMS 포함 제품 선택 가능 | 순간 방전 성능 확인 필요 |

현재 코드의 cutoff 기준 `9.9V`는 3S 기준 셀당 약 `3.3V`이므로 3S 배터리와 잘 맞는다.

## 구매 전 확인할 사양

배터리 구매 전 다음 항목을 확인한다.

- 전압: `3S`, `11.1V nominal`, 완충 `12.6V`
- 용량: 최소 `2200mAh` 이상 권장, 실제 주행 시간 목표에 따라 조정
- 방전율: 모터 최대 전류를 감당할 수 있는 C-rate 또는 최대 방전 전류
- 커넥터: 모터 드라이버/전원 분배와 맞는 커넥터인지 확인
- 보호회로: Li-ion pack은 BMS 포함 여부 확인
- 충전기: 배터리 타입에 맞는 전용 충전기 필요

현재 모터 정보 기준으로 배터리와 전원부는 최소 다음 조건을 만족해야 한다.

- 모터 2개 정격 전류 합계 `3A` 이상을 감당할 것
- RPi 5, ESP32, 센서류 전류를 추가로 감당할 것
- 출발/급정지/stall 상황의 순간 전류 여유를 둘 것
- 모터 드라이버가 모터 1개당 `1.5A` 정격 전류를 안정적으로 처리할 것

따라서 배터리 방전 전류는 단순히 `3A`에 맞추지 말고 여유를 두어 선정한다. 실제 모터 stall current가 확인되면 그 값을 기준으로 다시 계산해야 한다.

## 전원 구조 권장안

권장 전원 흐름은 다음과 같다.

```text
배터리
 ├─ 모터 드라이버 VM 입력
 ├─ DC-DC Buck 5V → Raspberry Pi 5
 └─ DC-DC Buck 5V 또는 3.3V → ESP32
```

중요 조건:

- ESP32, 모터 드라이버, RPi 5의 GND 기준은 공통으로 맞춘다.
- 모터 전원을 ESP32 핀에서 직접 공급하지 않는다.
- RPi 5는 전류 소모가 크므로 안정적인 5V 전원 모듈을 사용한다.
- 모터 노이즈가 ESP32/RPi 5에 영향을 주지 않도록 배선과 전원 분리를 고려한다.

## LiPo 전압 측정 계획

배터리가 확정되기 전까지 v7 펌웨어의 `currentBatteryVoltage = 12.0` 임시값은 유지한다. 배터리와 저항값이 확정되면 전압 분배 회로를 추가하고 `readBatteryVoltage()`로 교체한다.

추천 시작안:

```text
R1 = 100kΩ
R2 = 33kΩ
ADC 핀 후보 = GPIO35
```

단, 실제 ESP32 보드에서 GPIO35가 비어 있는지 먼저 확인해야 한다. 현재 `MQ135_PIN = 34`이므로 GPIO34는 사용하지 않는다.

## 구매 후 검증 절차

배터리 구매 후 다음 순서로 확인한다.

1. 멀티미터로 배터리 전압을 측정한다.
2. 전압 분배 회로 출력이 ESP32 ADC 허용 범위 안인지 확인한다.
3. ESP32가 출력하는 `BAT=` 값과 멀티미터 값을 비교한다.
4. `BAT <= 9.9V`일 때 `STATE=STOP`으로 전환되는지 확인한다.
5. 모터 구동 중 전압 강하가 발생해도 시스템이 불안정해지지 않는지 확인한다.

## 지금 할 수 있는 과업

배터리 구매 전에는 다음 작업을 우선한다.

- 모터 드라이버 전류 여유 검토
- 모터 stall current 확인
- RPi 5 전원 모듈 선정
- E-Stop 버튼 배선 확정
- 엔코더 `A/B` 입력 설계
- AMR 상태 전환 발표자료 정리

## 결정해야 할 항목

팀에서 다음 값을 확정해야 한다.

- 사용할 배터리 타입: LiPo 또는 Li-ion pack
- 배터리 용량
- 최대 방전 전류
- 커넥터 종류
- 충전기
- 전원 분배 방식
- ESP32 LiPo 측정 ADC 핀

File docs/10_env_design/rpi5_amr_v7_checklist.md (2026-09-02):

# RPi 5 - ESP32 #1 AMR v7 검증 체크리스트

## 큰 목표

이 체크리스트의 목표는 Raspberry Pi 5와 ESP32 #1 AMR v7이 안전하게 통신하는지 확인하는 것이다. 핵심은 RPi 5가 중앙 제어자 역할을 유지하고, ESP32 #1이 센서 오류, Emergency Stop, LiPo cutoff, 통신 timeout 상황에서 안전 상태로 전환되는지 검증하는 것이다.

## 준비물

- ESP32 #1 AMR 보드
- Raspberry Pi 5 또는 테스트용 PC
- USB Serial 케이블
- Arduino IDE
- Python 3
- `pyserial`

## 1. ESP32 업로드

Arduino IDE에서 다음 파일을 연다.

```text
Arduino/AMR_state_v7_ino/AMR_state_v7_ino.ino
```

ESP32 보드와 포트를 선택한 뒤 업로드한다. 업로드 후 Serial Monitor를 `115200 baud`로 연다.

## 2. RPi 5 Serial 포트 확인

RPi 5에서 ESP32가 어떤 포트로 잡혔는지 확인한다.

```bash
ls /dev/ttyUSB*
ls /dev/ttyACM*
```

대표 예시는 다음과 같다.

```text
/dev/ttyUSB0
/dev/ttyACM0
```

Windows PC에서 테스트한다면 장치 관리자 또는 Arduino IDE의 포트 목록에서 `COM5` 같은 포트를 확인한다.

## 3. pyserial 설치

RPi 5에서 실제 Serial 전송을 하려면 `pyserial`이 필요하다.

```bash
python3 -m pip install pyserial
```

설치가 제한된 환경이면 가상환경을 사용한다.

```bash
python3 -m venv .venv
source .venv/bin/activate
python -m pip install pyserial
```

## 4. keepalive 메시지 dry-run

실제 Serial을 쓰기 전에 메시지 형식만 확인한다.

```bash
python tools/rpi_keepalive.py --dry-run --count 2
```

예상 출력:

```text
<CMD,PING,76>
<CMD,PING,76>
```

`76`은 `CMD,PING` payload의 XOR checksum이다.

## 5. keepalive 실제 전송

RPi 5에서 ESP32 포트로 1초마다 keepalive를 보낸다.

```bash
python tools/rpi_keepalive.py --port /dev/ttyUSB0 --interval 1
```

Windows PC에서 테스트하면 포트 예시는 다음과 같다.

```powershell
python tools\rpi_keepalive.py --port COM5 --interval 1
```

## 6. 정상 통신 확인

ESP32 Serial Monitor에서 다음 형식의 메시지가 주기적으로 출력되는지 확인한다.

```text
<CMD,STATE=SAFE,GAS=...,FLAME=0,BAT=12.00,CS>
```

정상 기준:

- 메시지가 `<`로 시작하고 `>`로 끝난다.
- 첫 필드는 `CMD`다.
- `STATE=...`, `GAS=...`, `FLAME=...`, `BAT=...` 필드가 있다.
- 마지막 checksum 필드가 있다.

PC나 RPi 5에서 메시지 파싱만 먼저 확인하려면 다음 명령을 실행한다.

```bash
python tools/rpi_amr_parser.py "<CMD,STATE=SAFE,GAS=42,FLAME=0,BAT=12.00,56>"
```

예상 출력:

```text
command=CMD
state=SAFE
gas=42
flame=0
battery=12.0
```

## 7. timeout fallback 테스트

keepalive 실행을 중지한다. `RPI_TIMEOUT_MS = 3000`이므로 약 3초 뒤 ESP32 상태가 `STOP`으로 전환되어야 한다.

Pass 기준:

```text
STATE=STOP
```

Fail 기준:

- keepalive가 끊겼는데도 계속 `SAFE` 또는 `WARNING`을 유지한다.
- checksum이 틀린 메시지로 timeout이 해제된다.

## 8. Emergency Stop 테스트

E-Stop 입력은 현재 `EMERGENCY_STOP_PIN = 26`, `INPUT_PULLUP`, active-low 기준이다.

Pass 기준:

- GPIO 26이 LOW가 되면 즉시 `STATE=STOP`으로 전환된다.
- E-Stop은 gas, flame, timeout보다 우선한다.

주의:

- 실제 버튼 배선이 다르면 핀 번호 또는 active level을 조정해야 한다.

## 9. Sensor Error 테스트

MQ-135 입력이 유효 범위 밖으로 3회 연속 판단되면 `SENSOR_ERROR`로 전환되어야 한다.

Pass 기준:

```text
STATE=SENSOR_ERROR
```

## 10. 기록할 항목

검증 후 다음 값을 기록한다.

- ESP32 포트:
- RPi 5 포트:
- keepalive 주기:
- timeout 전환 시간:
- E-Stop 핀과 active level:
- MQ-135 정상 범위:
- Serial 출력 예시:

## 다음 개선 후보

- 실제 LiPo 전압 분배 회로 연결 및 ADC 변환 함수 구현
- `applyAmrAction()`에 실제 모터 드라이버 제어 연결
- RPi 5 keepalive를 systemd 서비스로 등록
- 발표용 상태 전환 다이어그램 작성

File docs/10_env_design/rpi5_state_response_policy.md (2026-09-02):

# RPi 5 AMR 상태 대응 정책

## 목적

이 문서는 Raspberry Pi 5가 ESP32 #1 AMR v7에서 받은 상태 메시지에 어떻게 대응해야 하는지 정리한다. ESP32 #1은 센서와 안전 조건을 바탕으로 AMR 상태를 판단하고, RPi 5는 그 결과를 중앙에서 해석해 전체 시스템 동작을 중재한다.

## 기본 원칙

- RPi 5는 ESP32 #1과 ESP32 #2를 각각 통신한다.
- ESP32 #1과 ESP32 #2가 직접 통신하는 구조를 만들지 않는다.
- ESP32 #1이 보내는 checksum이 맞는 메시지만 신뢰한다.
- `STOP`, `DANGER`, `SENSOR_ERROR`는 항상 안전 우선 상태로 처리한다.
- RPi 5는 ESP32 #1 AMR 상태를 ARM 동작 허용 여부 판단에도 반영할 수 있다.

## 입력 메시지

ESP32 #1 AMR v7은 다음 형식으로 상태를 전송한다.

```text
<CMD,STATE=SAFE,GAS=42,FLAME=0,BAT=12.00,56>
```

RPi 5는 먼저 다음을 확인한다.

1. `<`, `>` 프레임이 있는가?
2. checksum이 맞는가?
3. `STATE`, `GAS`, `FLAME`, `BAT` 필드가 있는가?
4. 숫자 필드가 정상 변환되는가?

파싱 테스트는 다음 명령으로 확인할 수 있다.

```bash
python tools/rpi_amr_parser.py "<CMD,STATE=SAFE,GAS=42,FLAME=0,BAT=12.00,56>"
```

## 상태별 대응 정책

| ESP32 #1 상태 | RPi 5 해석 | 권장 대응 |
|---|---|---|
| `SAFE` | 정상 감시 상태 | AMR 정상 운용 허용 |
| `WARNING` | 주의 상태 | 감속, 로그 기록, 사용자 표시 |
| `DANGER` | 위험 상태 | AMR 정지 유지, ARM 동작 제한 검토, 경고 표시 |
| `STOP` | 안전 정지 상태 | AMR 정지 유지, 원인 확인 전 재개 금지 |
| `SENSOR_ERROR` | 센서 fault 상태 | AMR 정지 유지, 센서/배선 점검 요구 |

## 상태별 세부 행동

### SAFE

RPi 5는 AMR이 정상 감시 상태라고 판단한다. 주행 명령, 경로 계획, ARM 협업 동작을 허용할 수 있다. 단, keepalive는 계속 보내야 한다.

### WARNING

가스 수치가 주의 기준에 들어온 상태다. RPi 5는 감속, 로그 기록, UI 표시 같은 완화 조치를 수행한다. 즉시 전체 정지를 요구하지는 않지만, 상태가 DANGER로 올라갈 가능성을 고려한다.

### DANGER

flame 감지 또는 gas danger 조건이 충족된 상태다. RPi 5는 AMR 정지를 유지하고, ARM 동작도 위험 환경에서 계속 수행해도 되는지 제한해야 한다. 사용자에게 경고를 표시하고 상태 회복 전 자동 재개를 피한다.

### STOP

Emergency Stop, LiPo cutoff, RPi timeout 같은 안전 정지 상태다. RPi 5는 AMR이 움직이지 않도록 유지해야 한다. STOP 원인이 해소되기 전에는 주행 명령을 보내지 않는다.

### SENSOR_ERROR

MQ-135 센서값이 유효 범위를 벗어난 상태다. RPi 5는 이 상태를 단순 정지가 아니라 fault로 기록한다. 센서 배선, 전원, ADC 입력 문제를 점검해야 한다.

## 통신 timeout 정책

RPi 5는 ESP32 #1로 주기적으로 keepalive를 보낸다.

```text
<CMD,PING,76>
```

ESP32 #1은 checksum이 맞는 framed 메시지를 받아야 timeout을 해제한다. RPi 5 쪽 권장 keepalive 주기는 `1초`다. ESP32 #1의 timeout 기준은 현재 `3초`다.

## 재개 조건

정지 상태에서 자동 재개할지 여부는 상태별로 다르게 본다.

| 상태 | 자동 재개 권장 여부 |
|---|---|
| `WARNING -> SAFE` | 가능 |
| `DANGER -> SAFE` | 신중. 사용자 확인 권장 |
| `STOP -> SAFE` | 원인 확인 후 재개 |
| `SENSOR_ERROR -> SAFE` | 센서 점검 후 재개 |

## 로그로 남길 항목

RPi 5는 상태 메시지를 받을 때 다음 값을 기록하는 것이 좋다.

- 수신 시간
- 상태 `STATE`
- 가스 값 `GAS`
- flame 값 `FLAME`
- 배터리 값 `BAT`
- checksum 검증 결과
- 상태 변화 여부

## 다음 구현 후보

- `tools/rpi_amr_parser.py`를 기반으로 Serial read loop 추가
- 상태 변화만 콘솔에 표시하는 RPi 모니터 도구 작성
- ROS2 Jazzy 노드로 확장
- `DANGER`, `STOP`, `SENSOR_ERROR` 수신 시 ARM 동작 제한 정책 연결

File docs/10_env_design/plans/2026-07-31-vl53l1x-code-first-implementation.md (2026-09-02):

# VL53L1X Code-First Integration Implementation Plan

> **For agentic workers:** REQUIRED SUB-SKILL: Use superpowers:subagent-driven-development (recommended) or superpowers:executing-plans to implement this plan task-by-task. Steps use checkbox (`- [ ]`) syntax for tracking.

**Goal:** Preserve the uploaded ESP32 #1 AMR v8 sketch and create a v9 sketch that reads an Adafruit VL53L1X, evaluates distance hazards, fails safely when the sensor is unavailable, and emits distance in checked telemetry.

**Architecture:** Keep the existing single-sketch v8 structure and create a separate v9 sketch. Add a small non-blocking VL53L1X adapter inside that sketch, then pass its last valid millimetre reading and debounced validity into the existing evaluation flow. Mirror the Arduino decision logic in the existing standalone Python harness style so distance thresholds, safety priority, protocol fields, and checksum can be verified before hardware is soldered.

**Tech Stack:** ESP32 Arduino, `Wire`, bundled `Adafruit_VL53L1X`, Python 3 pure-logic harness, PowerShell

## Global Constraints

- Work only on ESP32 #1 AMR.
- Do not modify `Arduino/AMR_state_v8_ino/AMR_state_v8_ino.ino`.
- Do not add ESP32 #2 ARM, servo, gripper, buzzer, or output-device logic.
- Preserve Emergency Stop as the highest-priority condition.
- Preserve the 3S LiPo cutoff at exactly `9.9V`.
- Preserve RPi timeout fallback at `3000ms`.
- Preserve the outer protocol format `<CMD,...,CS>\n`.
- Preserve decimal ASCII-sum-modulo-256 checksum behavior.
- Use GPIO21 for SDA and GPIO22 for SCL.
- Use VL53L1X I2C address `0x29` and a `50ms` timing budget.
- Never transmit a simulated distance as a real hardware reading.
- Do not add MQ-2 in this plan; it follows after its module output voltage is confirmed.

## File Map

- Create `Arduino/AMR_state_v9_ino/AMR_state_v9_ino.ino`: v8 behavior plus VL53L1X initialization, reading, validation, distance risk evaluation, debug output, and v9 telemetry.
- Create `tests/amr_v9/test_amr_v9_pure.py`: executable pure-logic model and source-contract checks for v9.
- Read only `Arduino/AMR_state_v8_ino/AMR_state_v8_ino.ino`: stable source used as the v9 baseline.
- Read only `tests/amr_v8/test_amr_v8_pure.py`: existing test-harness style used as the v9 baseline.

---

### Task 1: Add failing v9 distance and protocol tests

**Files:**
- Create: `tests/amr_v9/test_amr_v9_pure.py`
- Read: `tests/amr_v8/test_amr_v8_pure.py`
- Expected later source: `Arduino/AMR_state_v9_ino/AMR_state_v9_ino.ino`

**Interfaces:**
- Consumes: v8 enums, threshold behavior, checksum algorithm, and test-report format.
- Produces: `V9Context`, `update_distance_reading()`, `evaluate_amr_state()`, `determine_safety_fault()`, `build_sensor_message()`, and executable regression checks.

- [ ] **Step 1: Create the v9 pure-logic model**

Start from the v8 test harness structure, rename the context to `V9Context`, separate the two sensor error counters, and add these exact constants and functions:

```python
DISTANCE_INVALID_MM = -1
DISTANCE_MIN_VALID_MM = 30
DISTANCE_MAX_VALID_MM = 4000
DISTANCE_WARNING_ENTER_MM = 500
DISTANCE_WARNING_EXIT_MM = 550
DISTANCE_DANGER_ENTER_MM = 200
DISTANCE_DANGER_EXIT_MM = 250

@dataclass
class V9Context:
    danger_count: int = 0
    gas_sensor_error_count: int = 0
    distance_sensor_error_count: int = 0
    last_valid_distance_mm: int = DISTANCE_INVALID_MM

def update_distance_reading(raw_distance_mm, context):
    raw_valid = DISTANCE_MIN_VALID_MM <= raw_distance_mm <= DISTANCE_MAX_VALID_MM
    if raw_valid:
        context.distance_sensor_error_count = 0
        context.last_valid_distance_mm = raw_distance_mm
    else:
        context.distance_sensor_error_count += 1

    sensor_valid = (
        context.distance_sensor_error_count < SENSOR_ERROR_COUNT_THRESHOLD
    )
    return context.last_valid_distance_mm, sensor_valid

def is_distance_danger_enter(distance_mm):
    return DISTANCE_MIN_VALID_MM <= distance_mm <= DISTANCE_DANGER_ENTER_MM

def is_distance_danger_stay(distance_mm):
    return DISTANCE_MIN_VALID_MM <= distance_mm <= DISTANCE_DANGER_EXIT_MM

def is_distance_warning_enter(distance_mm):
    return DISTANCE_MIN_VALID_MM <= distance_mm <= DISTANCE_WARNING_ENTER_MM

def is_distance_warning_stay(distance_mm):
    return DISTANCE_MIN_VALID_MM <= distance_mm <= DISTANCE_WARNING_EXIT_MM
```

Change `is_gas_sensor_valid()` to update
`context.gas_sensor_error_count`. Extend `evaluate_amr_state()` with
`distance_mm` and `distance_sensor_valid`. Reject either sensor fault before
RPi timeout and use these exact combined hazard conditions:

```python
if not gas_sensor_valid or not distance_sensor_valid:
    return AmrState.SENSOR_ERROR

danger_enter_condition = (
    flame_detected
    or gas_average >= GAS_DANGER_ENTER_THRESHOLD
    or is_distance_danger_enter(distance_mm)
)
danger_stay_condition = (
    flame_detected
    or gas_average >= GAS_DANGER_EXIT_THRESHOLD
    or is_distance_danger_stay(distance_mm)
)
warning_stay_condition = (
    gas_average >= GAS_WARNING_EXIT_THRESHOLD
    or is_distance_warning_stay(distance_mm)
)
warning_enter_condition = (
    gas_average >= GAS_WARNING_ENTER_THRESHOLD
    or is_distance_warning_enter(distance_mm)
)
```

Extend `determine_safety_fault()` with `distance_sensor_valid` and return
`SafetyFault.SENSOR` when either sensor is invalid.

- [ ] **Step 2: Add distance to the test-side telemetry builder**

Use this exact payload order:

```python
def build_sensor_payload(
    state,
    action,
    fault,
    gas_average,
    flame_detected,
    battery_voltage,
    distance_mm,
):
    return (
        f"SENS,{gas_average},{1 if flame_detected else 0},"
        f"{battery_to_centivolts(battery_voltage)},"
        f"{state.value},{action.value},{fault.value},{distance_mm}"
    )
```

`build_sensor_message()` must append the decimal checksum and `>\n` exactly as
v8 does.

- [ ] **Step 3: Add concrete behavioral test cases**

Add test results for all of these exact cases:

```python
distance_cases = [
    ("T_DISTANCE_SAFE", 700, AmrState.SAFE),
    ("T_DISTANCE_WARNING", 350, AmrState.WARNING),
]

context = V9Context()
state = AmrState.SAFE
for _ in range(3):
    distance_mm, distance_valid = update_distance_reading(150, context)
    state = evaluate_amr_state(
        gas_average=1200,
        flame_detected=False,
        gas_sensor_valid=True,
        distance_mm=distance_mm,
        distance_sensor_valid=distance_valid,
        battery_voltage=12.0,
        emergency_stop_active=False,
        rpi_timeout_active=False,
        last_state=state,
        context=context,
    )
assert state == AmrState.DANGER

context = V9Context()
for _ in range(3):
    distance_mm, distance_valid = update_distance_reading(-1, context)
assert distance_mm == -1
assert not distance_valid

context = V9Context()
distance_mm, distance_valid = update_distance_reading(150, context)
for _ in range(2):
    distance_mm, distance_valid = update_distance_reading(-1, context)
assert distance_mm == 150
assert distance_valid
distance_mm, distance_valid = update_distance_reading(-1, context)
assert distance_mm == 150
assert not distance_valid

distance_mm, distance_valid = update_distance_reading(700, context)
assert distance_mm == 700
assert distance_valid
assert context.distance_sensor_error_count == 0

context = V9Context()
state = AmrState.SAFE
for _ in range(3):
    distance_mm, distance_valid = update_distance_reading(150, context)
    state = evaluate_amr_state(
        gas_average=1200,
        flame_detected=False,
        gas_sensor_valid=True,
        distance_mm=distance_mm,
        distance_sensor_valid=distance_valid,
        battery_voltage=12.0,
        emergency_stop_active=False,
        rpi_timeout_active=False,
        last_state=state,
        context=context,
    )
assert state == AmrState.DANGER

distance_mm, distance_valid = update_distance_reading(240, context)
state = evaluate_amr_state(
    gas_average=1200,
    flame_detected=False,
    gas_sensor_valid=True,
    distance_mm=distance_mm,
    distance_sensor_valid=distance_valid,
    battery_voltage=12.0,
    emergency_stop_active=False,
    rpi_timeout_active=False,
    last_state=state,
    context=context,
)
assert state == AmrState.DANGER

distance_mm, distance_valid = update_distance_reading(260, context)
state = evaluate_amr_state(
    gas_average=1200,
    flame_detected=False,
    gas_sensor_valid=True,
    distance_mm=distance_mm,
    distance_sensor_valid=distance_valid,
    battery_voltage=12.0,
    emergency_stop_active=False,
    rpi_timeout_active=False,
    last_state=state,
    context=context,
)
assert state == AmrState.WARNING
```

Add explicit priority cases proving:

```python
Emergency Stop > LiPo cutoff > either sensor error > RPi timeout > hazard
```

Add a telemetry case that splits the payload and checks:

```python
fields == ["SENS", "120", "1", "1200", "0", "0", "0", "350"]
len(fields) == 8
```

Add source checks for these exact strings in the future v9 sketch:

```python
'#include <Adafruit_VL53L1X.h>'
'const int I2C_SDA_PIN = 21;'
'const int I2C_SCL_PIN = 22;'
'const uint8_t VL53L1X_I2C_ADDRESS = 0x29;'
'distanceSensor.startRanging()'
'distanceSensor.setTimingBudget(VL53L1X_TIMING_BUDGET_MS)'
'payload += String(distanceMm);'
```

- [ ] **Step 4: Run the new harness and verify the expected failure**

Run:

```powershell
C:\Users\rkdgm\.cache\codex-runtimes\codex-primary-runtime\dependencies\python\python.exe tests\amr_v9\test_amr_v9_pure.py
```

Expected: FAIL because
`Arduino/AMR_state_v9_ino/AMR_state_v9_ino.ino` does not exist or because the
required VL53L1X source strings are absent.

- [ ] **Step 5: Commit the failing test harness**

```powershell
C:\Users\rkdgm\.cache\codex-runtimes\codex-primary-runtime\dependencies\native\git\cmd\git.exe add -- tests/amr_v9/test_amr_v9_pure.py
C:\Users\rkdgm\.cache\codex-runtimes\codex-primary-runtime\dependencies\native\git\cmd\git.exe commit -m "Add VL53L1X v9 logic tests"
```

---

### Task 2: Create the v9 Arduino sketch

**Files:**
- Create: `Arduino/AMR_state_v9_ino/AMR_state_v9_ino.ino`
- Read baseline: `Arduino/AMR_state_v8_ino/AMR_state_v8_ino.ino`
- Test: `tests/amr_v9/test_amr_v9_pure.py`

**Interfaces:**
- Consumes: v8 sensor/state/message functions and the thresholds established by Task 1.
- Produces: `initializeDistanceSensor()`, `readDistanceMm()`, `updateDistanceSensorValidity()`, distance-aware `evaluateAmrState()`, distance-aware `determineSafetyFault()`, and v9 telemetry.

- [ ] **Step 1: Create v9 from the complete v8 sketch**

Create `Arduino/AMR_state_v9_ino/AMR_state_v9_ino.ino` with the full v8 source
as its starting content. Change the file banner and startup strings from v8 to
v9. Do not edit the v8 file.

At the top of v9, use these includes:

```cpp
#include <Arduino.h>
#include <Wire.h>
#include <Adafruit_VL53L1X.h>
```

- [ ] **Step 2: Add exact I2C, sensor, and threshold constants**

Place these constants beside the existing pin and sensor settings:

```cpp
const int I2C_SDA_PIN = 21;
const int I2C_SCL_PIN = 22;
const uint8_t VL53L1X_I2C_ADDRESS = 0x29;
const int VL53L1X_TIMING_BUDGET_MS = 50;

const int DISTANCE_INVALID_MM = -1;
const int DISTANCE_MIN_VALID_MM = 30;
const int DISTANCE_MAX_VALID_MM = 4000;
const int DISTANCE_WARNING_ENTER_MM = 500;
const int DISTANCE_WARNING_EXIT_MM = 550;
const int DISTANCE_DANGER_ENTER_MM = 200;
const int DISTANCE_DANGER_EXIT_MM = 250;
```

Add these globals without changing the v8 gas sample storage:

```cpp
Adafruit_VL53L1X distanceSensor;
bool distanceSensorInitialized = false;
int distanceSensorErrorCount = 0;
int lastValidDistanceMm = DISTANCE_INVALID_MM;
```

Rename the existing `sensorErrorCount` to `gasSensorErrorCount` everywhere so
the two sensor failures remain isolated.

- [ ] **Step 3: Implement non-blocking sensor initialization and reading**

Add these declarations:

```cpp
void initializeDistanceSensor();
int readDistanceMm();
bool updateDistanceSensorValidity(int rawDistanceMm);
bool isDistanceDangerEnter(int distanceMm);
bool isDistanceDangerStay(int distanceMm);
bool isDistanceWarningEnter(int distanceMm);
bool isDistanceWarningStay(int distanceMm);
```

Implement initialization without an infinite retry:

```cpp
void initializeDistanceSensor() {
  Wire.begin(I2C_SDA_PIN, I2C_SCL_PIN);

  if (!distanceSensor.begin(VL53L1X_I2C_ADDRESS, &Wire)) {
    distanceSensorInitialized = false;
    Serial.print("[VL53L1X] INIT_ERROR=");
    Serial.println(distanceSensor.vl_status);
    return;
  }

  if (!distanceSensor.startRanging()) {
    distanceSensorInitialized = false;
    Serial.print("[VL53L1X] RANGE_START_ERROR=");
    Serial.println(distanceSensor.vl_status);
    return;
  }

  if (!distanceSensor.setTimingBudget(VL53L1X_TIMING_BUDGET_MS)) {
    distanceSensorInitialized = false;
    Serial.print("[VL53L1X] TIMING_ERROR=");
    Serial.println(distanceSensor.vl_status);
    return;
  }

  distanceSensorInitialized = true;
  Serial.println("[VL53L1X] READY");
}
```

Implement one non-blocking read:

```cpp
int readDistanceMm() {
  if (!distanceSensorInitialized || !distanceSensor.dataReady()) {
    return DISTANCE_INVALID_MM;
  }

  int distanceMm = distanceSensor.distance();
  bool interruptCleared = distanceSensor.clearInterrupt();

  if (
    !interruptCleared ||
    distanceMm < DISTANCE_MIN_VALID_MM ||
    distanceMm > DISTANCE_MAX_VALID_MM
  ) {
    return DISTANCE_INVALID_MM;
  }

  return distanceMm;
}

bool updateDistanceSensorValidity(int rawDistanceMm) {
  bool rawValid = (
    rawDistanceMm >= DISTANCE_MIN_VALID_MM &&
    rawDistanceMm <= DISTANCE_MAX_VALID_MM
  );

  if (rawValid) {
    lastValidDistanceMm = rawDistanceMm;
    distanceSensorErrorCount = 0;
  } else {
    distanceSensorErrorCount++;
  }

  return distanceSensorErrorCount < SENSOR_ERROR_COUNT_THRESHOLD;
}
```

Add the four threshold helpers as inclusive integer comparisons matching
Task 1.

- [ ] **Step 4: Initialize and sample VL53L1X in the existing flow**

Call `initializeDistanceSensor()` in `setup()` after the existing pin modes
and before the startup telemetry.

In the 300ms read block, add:

```cpp
int rawDistanceMm = readDistanceMm();
bool distanceSensorValid = updateDistanceSensorValidity(rawDistanceMm);
int distanceMm = lastValidDistanceMm;
```

Pass `distanceMm` and `distanceSensorValid` into state evaluation, fault
selection, heartbeat telemetry, state-change telemetry, and debug output.

- [ ] **Step 5: Extend safety evaluation without weakening v8 priorities**

Extend the relevant signatures with:

```cpp
int distanceMm,
bool distanceSensorValid
```

Immediately after the LiPo check, use:

```cpp
if (!gasSensorValid || !distanceSensorValid) {
  return STATE_SENSOR_ERROR;
}
```

Use these conditions:

```cpp
bool dangerEnterCondition = (
  flameDetected ||
  gasAverage >= GAS_DANGER_ENTER_THRESHOLD ||
  isDistanceDangerEnter(distanceMm)
);

bool dangerStayCondition = (
  flameDetected ||
  gasAverage >= GAS_DANGER_EXIT_THRESHOLD ||
  isDistanceDangerStay(distanceMm)
);

bool warningStayCondition = (
  gasAverage >= GAS_WARNING_EXIT_THRESHOLD ||
  isDistanceWarningStay(distanceMm)
);

bool warningEnterCondition = (
  gasAverage >= GAS_WARNING_ENTER_THRESHOLD ||
  isDistanceWarningEnter(distanceMm)
);
```

Replace the existing gas-only WARNING checks with
`warningStayCondition` and `warningEnterCondition`. In
`determineSafetyFault()`, return `FAULT_SENSOR` when either sensor validity
flag is false.

- [ ] **Step 6: Extend telemetry and debug output**

Extend `buildSensorPayload()` and `sendSensorMessage()` with `int distanceMm`.
After appending `faultCode`, append:

```cpp
payload += ",";
payload += String(distanceMm);
```

Update the protocol banner to:

```text
<SENS,gas,flame,battCv,stateCode,actionCode,faultCode,distanceMm,checksum>
```

Add these debug fields:

```cpp
Serial.print(" | DIST=");
if (distanceMm == DISTANCE_INVALID_MM) {
  Serial.print("INVALID");
} else {
  Serial.print(distanceMm);
  Serial.print("mm");
}

Serial.print(" | DIST_SENSOR=");
Serial.print(distanceSensorValid ? "OK" : "ERROR");

Serial.print(" | DIST_ERROR_COUNT=");
Serial.print(distanceSensorErrorCount);
```

- [ ] **Step 7: Run v9 and v8 pure-logic tests**

Run:

```powershell
C:\Users\rkdgm\.cache\codex-runtimes\codex-primary-runtime\dependencies\python\python.exe tests\amr_v9\test_amr_v9_pure.py
C:\Users\rkdgm\.cache\codex-runtimes\codex-primary-runtime\dependencies\python\python.exe tests\amr_v8\test_amr_v8_pure.py
```

Expected: both commands exit `0`; the v9 report contains no `FAIL`, and the
v8 regression report remains unchanged.

- [ ] **Step 8: Commit the v9 sketch**

```powershell
C:\Users\rkdgm\.cache\codex-runtimes\codex-primary-runtime\dependencies\native\git\cmd\git.exe add -- Arduino/AMR_state_v9_ino/AMR_state_v9_ino.ino
C:\Users\rkdgm\.cache\codex-runtimes\codex-primary-runtime\dependencies\native\git\cmd\git.exe commit -m "Add VL53L1X AMR v9 integration"
```

---
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

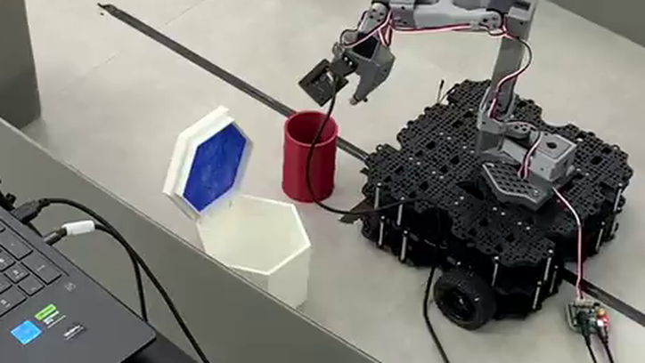
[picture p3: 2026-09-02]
report/빌드/img/grip1.png

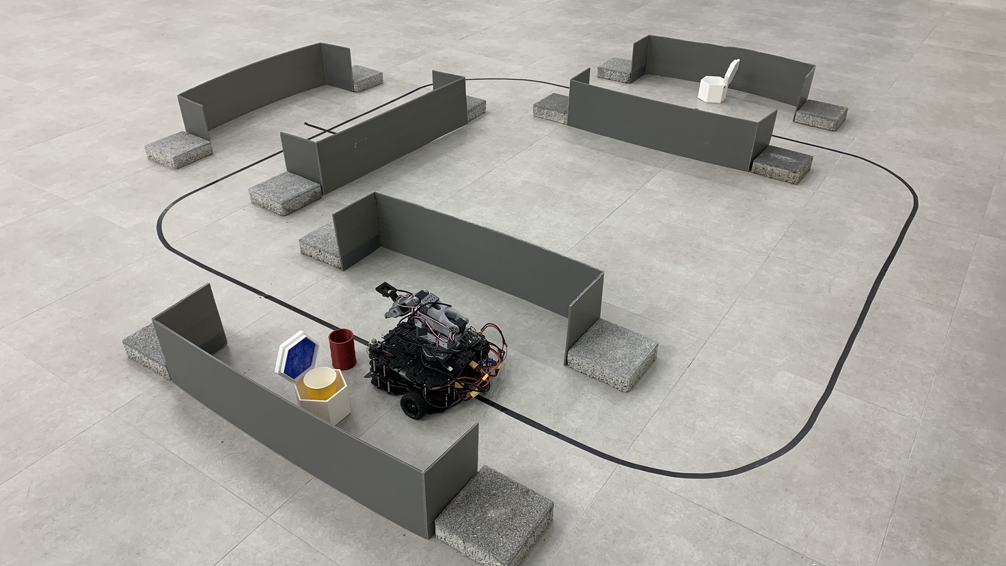
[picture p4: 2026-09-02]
report/빌드/img/demo_space.png

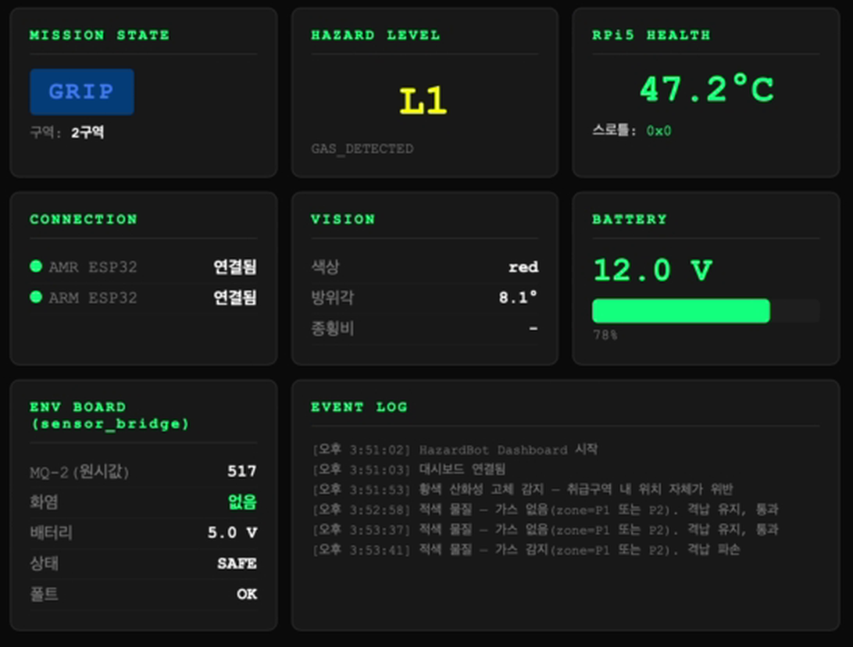
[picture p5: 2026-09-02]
report/빌드/img/dash_full.png

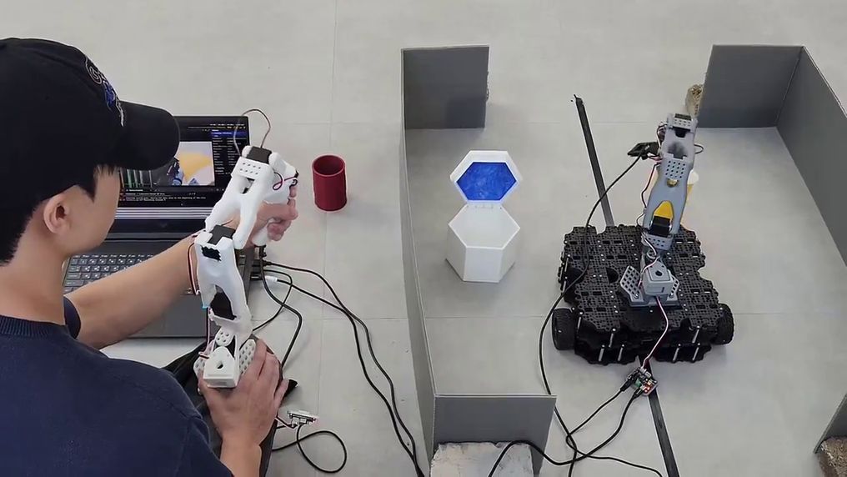
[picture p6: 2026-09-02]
report/빌드/img/act_collect.png

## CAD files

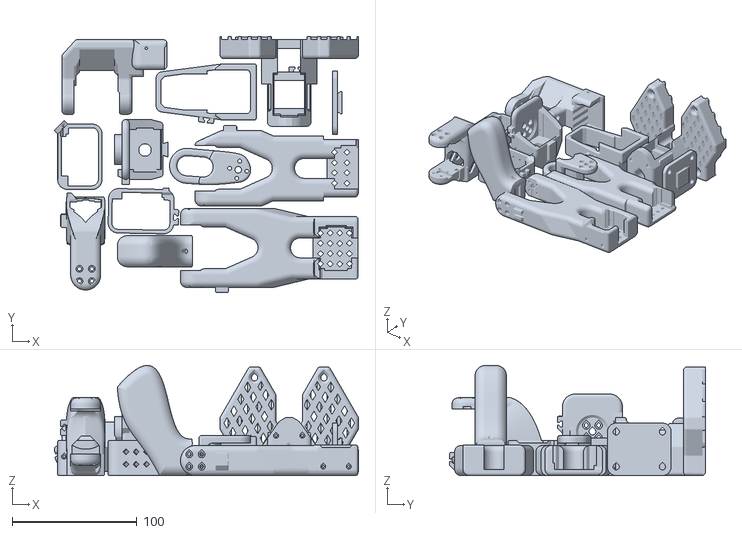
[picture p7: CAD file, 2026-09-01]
hardware/Leader_SO101.stl
243.4 x 204.7 x 88.1

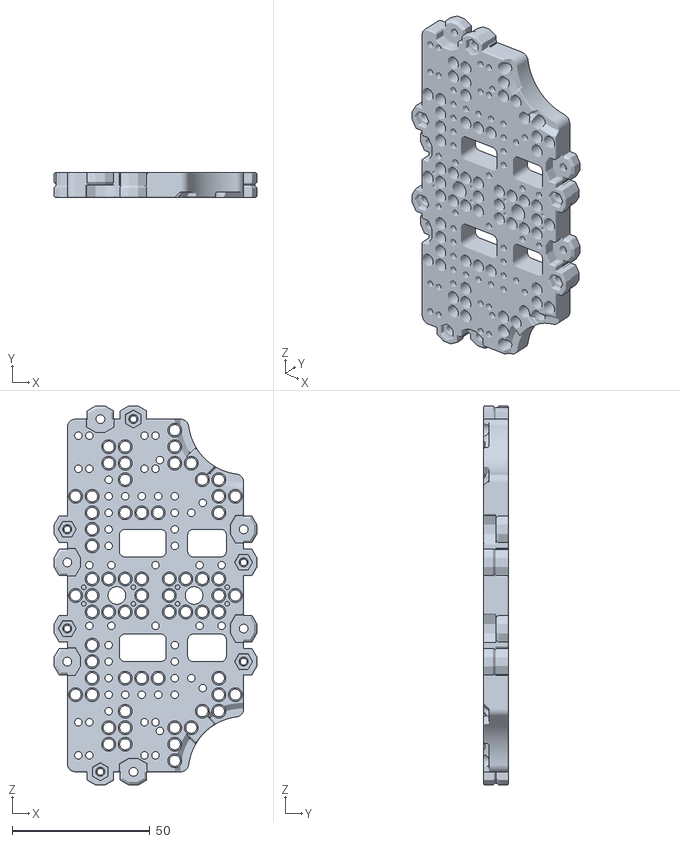
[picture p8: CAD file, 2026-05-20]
hardware/Waffle_Plate.stl
73.5 x 9.00 x 137.5

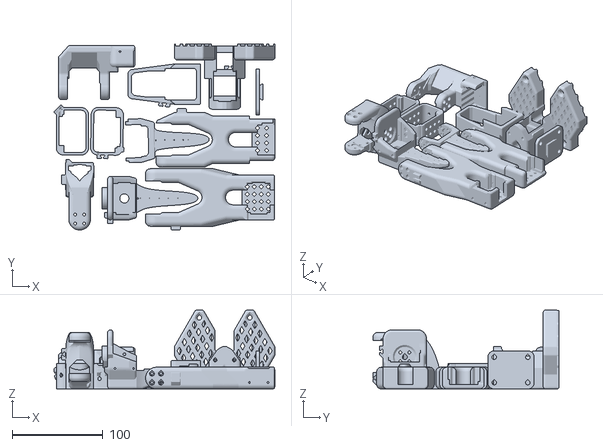
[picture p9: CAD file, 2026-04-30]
hardware/Follower_SO101.stl
243.4 x 204.9 x 87.0

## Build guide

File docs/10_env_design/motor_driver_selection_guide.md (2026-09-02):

# AMR 모터 드라이버 선정 기준

## 목적

이 문서는 HazardBot AMR의 DC 12V 구동 모터에 맞는 모터 드라이버 선정 기준을 정리한다. 현재 보유한 `keyestudio TB6612FNG Motor Driver for Arduino`는 모터 드라이버가 맞지만, 현재 모터 정격 전류 기준으로 최종 주행용으로는 전류 여유가 부족할 수 있다.

## 현재 모터 조건

ICBANQ 제품 정보 기준 모터 사양:

| 항목 | 값 |
|---|---|
| 모델 | CHR-GM25-370 / CHIHAI MOTOR |
| 구동 전압 | DC 12V |
| 정격 전류 | 1.5A |
| 속도 | 350rpm |
| 토크 | 3.5kg.cm |
| 타이어 직경 | 130mm |
| 타이어 폭 | 60mm |

좌우 구동을 위해 모터 2개를 사용하면 정격 전류만 합산해도 약 `3.0A`가 필요하다. 출발, 회전, 바퀴 걸림, stall 상황에서는 이보다 큰 순간 전류가 흐를 수 있다.

## TB6612FNG 판단

TB6612FNG는 소형 DC 모터용 드라이버로는 적합하지만, 현재 AMR 바퀴 구동 모터에는 여유가 작다.

| 항목 | 판단 |
|---|---|
| 전압 | 12V 모터와 대체로 호환 가능 |
| 정격 전류 | 모터 1개당 1.5A라 여유 부족 가능 |
| stall current | 미확인. TB6612FNG 한계를 넘을 수 있음 |
| 사용 권장 | 저부하 짧은 테스트까지만 권장 |
| 최종 주행 | 더 큰 전류 드라이버 검토 권장 |

## 새 드라이버 권장 조건

최종 AMR 주행용 드라이버는 최소 다음 조건을 만족하는 것이 좋다.

| 항목 | 권장 기준 |
|---|---|
| 모터 전압 | 12V 이상 지원 |
| 채널 수 | DC 모터 2개 이상 |
| 채널당 연속 전류 | 최소 2A 이상, 권장 3A 이상 |
| 채널당 피크 전류 | 최소 5A 이상 권장 |
| 제어 방식 | ESP32 PWM 제어 가능 |
| 로직 전압 | 3.3V 입력 호환 또는 level shifting 필요 |
| 보호 기능 | 과전류, 과열, 역전압 보호 권장 |
| 방열 | 방열판 또는 충분한 PCB 방열 면적 권장 |

정격 전류 `1.5A` 모터는 실제 주행 중 순간적으로 더 큰 전류를 요구할 수 있으므로, 드라이버를 정격값에 딱 맞춰 고르지 말고 여유를 둔다.

## 후보 드라이버를 볼 때 확인할 항목

제품 페이지나 데이터시트에서 다음 항목을 확인한다.

- `Motor supply voltage`
- `Continuous current per channel`
- `Peak current per channel`
- `Logic input voltage`
- `PWM frequency`
- `Control interface`
- `Thermal shutdown`
- `Overcurrent protection`
- `Number of motor channels`

## 제어 방식별 코드 영향

모터 드라이버 제어 방식에 따라 `applyAmrAction()`에 들어갈 코드 구조가 달라진다.

### PWM/DIR 방식

핀 예시:

```text
LEFT_PWM, LEFT_DIR
RIGHT_PWM, RIGHT_DIR
```

특징:

- 속도는 PWM으로 제어
- 방향은 DIR 핀으로 제어
- 코드가 비교적 단순함

### IN1/IN2 방식

핀 예시:

```text
LEFT_IN1, LEFT_IN2
RIGHT_IN1, RIGHT_IN2
```

특징:

- IN1/IN2 조합으로 방향과 정지를 제어
- PWM을 한쪽 입력에 걸거나 enable 핀에 걸 수 있음
- 드라이버별 동작표 확인 필요

## 상태별 action 연결 원칙

현재 v7의 action 분류는 유지한다.

| 상태 | Action | 모터 출력 원칙 |
|---|---|---|
| `SAFE` | `NORMAL_MOTION` | 정상 속도 허용 |
| `WARNING` | `LIMITED_MOTION` | 감속 또는 제한 출력 |
| `DANGER` | `STOP_MOTION` | 모터 정지 |
| `STOP` | `STOP_MOTION` | 모터 정지 |
| `SENSOR_ERROR` | `STOP_MOTION` | 모터 정지 |

실제 모터 제어를 추가할 때도 Emergency Stop, LiPo cutoff, timeout, sensor error 조건은 항상 모터 정지보다 우선해야 한다.

## 구매 전 체크리스트

새 모터 드라이버를 구매하기 전에 다음을 확인한다.

- 모터 2개를 동시에 구동할 수 있는가?
- 채널당 연속 전류가 최소 `2A`, 가능하면 `3A` 이상인가?
- 피크 전류가 stall 상황을 어느 정도 감당할 수 있는가?
- 12V 배터리와 호환되는가?
- ESP32 3.3V GPIO로 제어 가능한가?
- 방열 대책이 있는가?
- 제어 핀 수가 ESP32에서 확보 가능한가?
- 제품 문서에 truth table 또는 제어 예제가 있는가?

## 추천 결정

현재 TB6612FNG는 보유 부품이므로 회로 이해나 무부하 테스트에는 사용할 수 있다. 하지만 실제 130mm 타이어를 장착한 AMR 주행에서는 전류 여유가 부족할 수 있으므로, 최종 구동용으로는 더 높은 전류 등급의 드라이버를 선정하는 것이 안전하다.

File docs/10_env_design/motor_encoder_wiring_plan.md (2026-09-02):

# AMR 모터 및 엔코더 배선 설계 메모

## 목적

이 문서는 현재 보유한 `DC 12V 350rpm` 모터 세트의 단자 역할을 정리하고, ESP32 #1 AMR에서 모터 드라이버와 엔코더를 어떻게 분리해 다룰지 설계한다. 아직 실제 모터 구동 코드는 추가하지 않는다.

## 현재 확인된 모터 정보

모터 연결부에는 다음 6개 표기가 있다.

```text
M2, V, A, B, G, M1
```

이는 일반적인 DC 감속모터 + 엔코더 구성일 가능성이 높다.

ICBANQ 제품 정보 기준으로 확인된 모터/타이어 사양은 다음과 같다.

| 항목 | 값 |
|---|---|
| 모터 모델 | CHR-GM25-370 / CHIHAI MOTOR DC GEAR MOTOR |
| 구동 전압 | DC 12V |
| 정격 전류 | 1.5A |
| 속도 | 350rpm |
| 토크 | 3.5kg.cm |
| 샤프트 길이 | 12mm |
| 샤프트 직경 | 4mm |
| 타이어 직경 | 130mm |
| 타이어 폭 | 60mm |
| 타이어 내경 | 육각 12mm |

| 표기 | 추정 역할 | 연결 대상 |
|---|---|---|
| `M1` | 모터 전원 단자 1 | 모터 드라이버 출력 |
| `M2` | 모터 전원 단자 2 | 모터 드라이버 출력 |
| `V` | 엔코더 전원 + | 3.3V 또는 5V, 부품 사양 확인 필요 |
| `G` | 엔코더 GND | ESP32 GND와 공통 |
| `A` | 엔코더 채널 A | ESP32 입력 핀 |
| `B` | 엔코더 채널 B | ESP32 입력 핀 |

주의: 실제 제품에 따라 `V`가 5V 전용일 수 있다. 엔코더 출력이 5V이면 ESP32 입력에 직접 넣으면 안 되고 level shifting 또는 3.3V 호환 여부 확인이 필요하다.

## 모터 드라이버가 필요한 이유

ESP32 GPIO는 모터를 직접 구동할 수 없다. `M1`, `M2`는 반드시 모터 드라이버의 출력 단자에 연결해야 한다.

기본 연결 구조:

```text
배터리 +  ── 모터 드라이버 VM
배터리 -  ── 모터 드라이버 GND
ESP32 GND ── 모터 드라이버 GND

모터 드라이버 OUT1 ── M1
모터 드라이버 OUT2 ── M2
```

ESP32는 모터 드라이버의 `PWM`, `DIR`, `IN1`, `IN2` 같은 제어 핀만 제어한다. 실제 모터 전류는 드라이버가 담당한다.

## TB6612FNG 사용 가능성 판단

현재 보유한 드라이버는 `keyestudio TB6612FNG Motor Driver for Arduino`이다. 이 부품은 DC 모터 드라이버가 맞다. 다만 현재 모터의 정격 전류가 `1.5A`이므로 TB6612FNG를 최종 주행용 드라이버로 쓰기에는 전류 여유가 부족할 가능성이 크다.

판단 기준:

| 항목 | 판단 |
|---|---|
| 전압 | 모터 12V이므로 TB6612FNG 전압 범위와 대체로 맞음 |
| 정격 전류 | 모터 1개당 1.5A로 TB6612FNG 연속 전류 한계에 가까움 또는 초과 가능 |
| stall current | 아직 미확인. 정격 전류보다 훨씬 클 가능성이 있음 |
| 최종 주행용 적합성 | 보류. 더 큰 전류 여유의 드라이버 검토 권장 |

따라서 TB6612FNG는 낮은 부하의 짧은 기능 테스트에는 사용할 수 있지만, AMR 바퀴 구동 최종안으로 확정하기 전에는 발열, 전압강하, stall current를 반드시 확인해야 한다.

권장 조건:

- 모터 1개당 연속 전류 `1.5A` 이상을 안정적으로 처리할 수 있을 것
- stall current를 감당할 피크 전류 여유가 있을 것
- 좌우 모터 2개를 동시에 구동할 때도 과열되지 않을 것
- 12V 배터리 전압과 호환될 것

## 엔코더 입력 구조

엔코더 `A`, `B` 신호는 회전 방향과 속도를 알기 위한 입력이다.

권장 구조:

```text
V  ── 엔코더 전원
G  ── ESP32 GND
A  ── ESP32 interrupt-capable input
B  ── ESP32 interrupt-capable input
```

엔코더를 통해 나중에 할 수 있는 일:

- 좌우 바퀴 속도 측정
- 직진 보정
- 회전량 추정
- 모터 stall 감지
- 주행 거리 추정

## ESP32 핀 선정 시 주의점

현재 v7에서 이미 사용하는 핀:

| 기능 | 핀 |
|---|---|
| MQ-135 | GPIO34 |
| Flame sensor | GPIO27 |
| Emergency Stop | GPIO26 |

LiPo 측정 후보로는 GPIO35를 고려 중이다. 따라서 엔코더 A/B는 위 핀과 겹치지 않게 정해야 한다.

권장 후보는 실제 보드 핀맵을 확인한 뒤 정한다. 엔코더 입력은 빠른 변화가 있으므로 interrupt 사용 가능 여부를 확인하는 것이 좋다.

## 상태별 모터 action과 연결

현재 v7에는 실제 모터 제어 대신 action 분류만 있다.

| 상태 | Action | 모터 의미 |
|---|---|---|
| `SAFE` | `NORMAL_MOTION` | 정상 주행 가능 |
| `WARNING` | `LIMITED_MOTION` | 감속 또는 제한 주행 |
| `DANGER` | `STOP_MOTION` | 정지 |
| `STOP` | `STOP_MOTION` | 정지 |
| `SENSOR_ERROR` | `STOP_MOTION` | 정지 |

나중에 실제 모터 제어를 붙일 때는 `applyAmrAction()` 안에서 action별 모터 출력을 제한한다.

## 실제 구현 전 확인할 것

아래 정보가 확정되어야 모터 제어 코드를 안전하게 추가할 수 있다.

- 사용하는 모터 드라이버 모델
- 모터 1개당 정격 전류와 stall current
- 모터 드라이버의 최대 전류
- 모터 드라이버 제어 방식: `PWM/DIR`인지 `IN1/IN2`인지
- 엔코더 전원 전압: 3.3V 호환인지 5V 전용인지
- 엔코더 A/B 출력 전압
- 사용할 ESP32 핀

## 하드웨어 없이 지금 할 수 있는 테스트

- `determineAmrAction()`이 상태별 action을 올바르게 반환하는지 확인한다.
- `DANGER`, `STOP`, `SENSOR_ERROR`가 모두 `STOP_MOTION`인지 확인한다.
- 나중에 모터 제어 함수를 추가하기 전에도 action hook이 독립적으로 유지되는지 확인한다.

현재 Python 하네스는 이 action mapping을 검증한다.

## 실제 보드에서 확인할 항목

- 모터 드라이버 없이 ESP32에 모터를 직접 연결하지 않았는가?
- 모터 드라이버 GND와 ESP32 GND가 공통인가?
- 엔코더 V 전압이 ESP32 입력 허용 범위와 맞는가?
- 바퀴를 손으로 돌렸을 때 A/B 신호가 변하는가?
- 모터 구동 중 ESP32 reset이나 Serial 끊김이 없는가?

## 추천 다음 단계

1. 모터 드라이버 모델명을 확인한다.
2. 모터 드라이버 제어 핀 표기를 확인한다.
3. 엔코더 V/A/B/G 전압을 제품 문서나 멀티미터로 확인한다.
4. ESP32에서 사용할 엔코더 입력 핀 후보를 정한다.
5. 그 다음에야 `applyAmrAction()`에 실제 모터 제어를 연결한다.

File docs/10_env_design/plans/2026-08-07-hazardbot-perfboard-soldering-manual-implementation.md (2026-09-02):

# HazardBot Perfboard Soldering Manual Implementation Plan

> **For agentic workers:** REQUIRED SUB-SKILL: Use superpowers:subagent-driven-development (recommended) or superpowers:executing-plans to implement this plan task-by-task. Steps use checkbox (`- [ ]`) syntax for tracking.

**Goal:** Produce a visually verified Korean A4 PDF that teaches a complete beginner how to solder the HazardBot sensor and drive perfboards one action at a time.

**Architecture:** Store the approved Korean copy and wiring nets as validated Python data, render reusable vector diagrams with ReportLab, and assemble the manual with a dedicated PDF builder. Verify the generated PDF structurally with Python and visually by rendering every page to PNG before delivery.

**Tech Stack:** Python 3, ReportLab, pypdf, pdfplumber, Poppler PDF rendering, `unittest`, PowerShell

## Global Constraints

- Output one printable A4 PDF containing clearly separated sensor-board and drive-board sections.
- Write for a reader with no soldering experience and a reading level suitable for a 12-year-old.
- Explain each physical action separately: setup, hand/tool position, action, correct result, common mistake, and checkpoint.
- Use exact wiring from `docs/superpowers/specs/2026-08-07-hazardbot-perfboard-soldering-manual-design.md`.
- Use two single-sided 100×100mm, 2.54mm perfboards and four 20-pin female headers trimmed to 19 pins.
- Use existing resistors and jumper wires; do not make additional purchases mandatory.
- Use the four female headers only for the two 38-pin ESP32 boards.
- Keep TB6612FNG VM, power GND, A01/A02, and B01/B02 outside the thin logic rails and preserve the already-tested direct wiring.
- Mark hot-iron, power-on, and motor-power work as requiring teacher or adult supervision.
- Use both color and repeated net labels so the guide remains usable when actual jumper colors differ.
- Render and inspect every PDF page before claiming completion.

## File Structure

- Create `tools/soldering_manual/content.py`: approved Korean copy, wiring nets, page-section definitions, and consistency validation.
- Create `tools/soldering_manual/diagrams.py`: reusable ReportLab vector diagrams for board faces, holder orientation, solder joints, rails, dividers, and power boundaries.
- Create `tools/soldering_manual/build_manual.py`: A4 layout, typography, page headers/footers, tables, callouts, and final PDF assembly.
- Create `tests/soldering_manual/test_manual.py`: pin-map, required-section, diagram-registry, PDF page-count, and text-extraction checks.
- Create `docs/guides/HazardBot_만능기판_납땜_설명서.pdf`: final user-facing PDF.
- Create `tmp/soldering-manual-render/`: rendered PNG pages and contact sheet used only for visual QA.

---

### Task 1: Lock the Manual Content and Wiring Nets

**Files:**
- Create: `tools/soldering_manual/content.py`
- Create: `tests/soldering_manual/test_manual.py`
- Reference: `docs/superpowers/specs/2026-08-07-hazardbot-perfboard-soldering-manual-design.md`
- Reference: `docs/중요/README.md`

**Interfaces:**
- Produces: `MANUAL_TITLE: str`, `SECTIONS: tuple[dict, ...]`, `SENSOR_NETS: tuple[tuple[str, str], ...]`, `DRIVE_NETS: tuple[tuple[str, str], ...]`, `COLOR_LEGEND: dict[str, str]`, and `validate_content() -> None`.
- Consumes: no generated files.

- [ ] **Step 1: Write failing content tests**

Create `tests/soldering_manual/test_manual.py` with exact assertions for the approved wiring and required sections:

```python
import sys
import unittest
from pathlib import Path

ROOT = Path(__file__).resolve().parents[2]
sys.path.insert(0, str(ROOT))

from tools.soldering_manual import content

class ManualContentTests(unittest.TestCase):
    def test_sensor_nets_match_v10_wiring(self):
        self.assertIn(("MQ-135 AO", "10kΩ → GPIO34 중점; 20kΩ → GND"), content.SENSOR_NETS)
        self.assertIn(("MQ-2 AO", "10kΩ → GPIO35 중점; 20kΩ → GND"), content.SENSOR_NETS)
        self.assertIn(("KY-026 DO", "GPIO27"), content.SENSOR_NETS)
        self.assertIn(("VL53L1X SDA/SCL", "GPIO21/GPIO22"), content.SENSOR_NETS)

    def test_drive_nets_match_confirmed_wiring(self):
        required = {
            ("PWMA", "GPIO25"), ("AIN1/AIN2", "GPIO26/GPIO27"),
            ("PWMB", "GPIO14"), ("BIN1/BIN2", "GPIO16/GPIO17"),
            ("STBY", "GPIO4"), ("S1/S2/S3/S4/S5", "GPIO13/18/19/23/32"),
        }
        self.assertTrue(required.issubset(set(content.DRIVE_NETS)))

    def test_manual_has_separate_board_sections_and_checklist(self):
        ids = {section["id"] for section in content.SECTIONS}
        self.assertTrue({"basics", "sensor_board", "drive_board", "final_check"}.issubset(ids))

    def test_content_validation_passes(self):
        content.validate_content()

if __name__ == "__main__":
    unittest.main()
```

- [ ] **Step 2: Run the test and confirm the expected failure**

Run:

```powershell
C:\Users\rkdgm\.cache\codex-runtimes\codex-primary-runtime\dependencies\python\python.exe tests\soldering_manual\test_manual.py
```

Expected: `ModuleNotFoundError: No module named 'tools.soldering_manual'`.

- [ ] **Step 3: Implement the approved content model**

Create `tools/soldering_manual/content.py` with immutable tuples and a validation function. Include all approved sections and use these exact core nets:

```python
MANUAL_TITLE = "HazardBot 만능기판 납땜 설명서"

SENSOR_NETS = (
    ("5V 레일", "ESP32 5V/VIN → MQ-135 VCC, MQ-2 VCC"),
    ("3.3V 레일", "ESP32 3V3 → KY-026 VCC, VL53L1X VIN"),
    ("GND 레일", "ESP32 GND → 센서 4개 GND, 두 20kΩ 저항"),
    ("MQ-135 AO", "10kΩ → GPIO34 중점; 20kΩ → GND"),
    ("MQ-2 AO", "10kΩ → GPIO35 중점; 20kΩ → GND"),
    ("KY-026 DO", "GPIO27"),
    ("VL53L1X SDA/SCL", "GPIO21/GPIO22"),
)

DRIVE_NETS = (
    ("PWMA", "GPIO25"),
    ("AIN1/AIN2", "GPIO26/GPIO27"),
    ("PWMB", "GPIO14"),
    ("BIN1/BIN2", "GPIO16/GPIO17"),
    ("STBY", "GPIO4"),
    ("TB6612 VCC/logic GND", "ESP32 3V3/GND"),
    ("S1/S2/S3/S4/S5", "GPIO13/18/19/23/32"),
    ("라인센서 VCC/GND", "ESP32 3V3/GND"),
)
```

`validate_content()` must reject duplicate section IDs, missing required section IDs, duplicate left-hand net names, and any text that routes `VM`, `A01`, `A02`, `B01`, or `B02` through a logic rail.

- [ ] **Step 4: Run the content tests**

Run the same command as Step 2.

Expected: four tests pass and exit code is `0`.

- [ ] **Step 5: Commit the validated content**

```powershell
git add tools\soldering_manual\content.py tests\soldering_manual\test_manual.py
git commit -m "Add soldering manual content model"
```

---

### Task 2: Build Reusable Beginner-Friendly Diagrams

**Files:**
- Create: `tools/soldering_manual/diagrams.py`
- Modify: `tests/soldering_manual/test_manual.py`

**Interfaces:**
- Consumes: `COLOR_LEGEND` from `tools.soldering_manual.content`.
- Produces: `DIAGRAMS: dict[str, Callable[[], Drawing]]` and `get_diagram(name: str) -> Drawing`.
- Required diagram names: `board_faces`, `holder_position`, `iron_contact`, `good_bad_joints`, `header_cut`, `header_alignment`, `rail_cross_section`, `sensor_top`, `sensor_bottom`, `mq_dividers`, `drive_top`, `drive_bottom`, `motor_power_boundary`, `power_on_sequence`.

- [ ] **Step 1: Add failing diagram-registry tests**

Append to `tests/soldering_manual/test_manual.py`:

```python
from tools.soldering_manual import diagrams

class ManualDiagramTests(unittest.TestCase):
    def test_all_required_diagrams_exist_and_have_size(self):
        required = {
            "board_faces", "holder_position", "iron_contact", "good_bad_joints",
            "header_cut", "header_alignment", "rail_cross_section", "sensor_top",
            "sensor_bottom", "mq_dividers", "drive_top", "drive_bottom",
            "motor_power_boundary", "power_on_sequence",
        }
        self.assertEqual(required, set(diagrams.DIAGRAMS))
        for name in required:
            drawing = diagrams.get_diagram(name)
            self.assertGreaterEqual(drawing.width, 240)
            self.assertGreaterEqual(drawing.height, 120)
```

- [ ] **Step 2: Run tests and verify the diagram import fails**

Run:

```powershell
C:\Users\rkdgm\.cache\codex-runtimes\codex-primary-runtime\dependencies\python\python.exe tests\soldering_manual\test_manual.py
```

Expected: import failure for `tools.soldering_manual.diagrams`.

- [ ] **Step 3: Implement diagram primitives**

Create `tools/soldering_manual/diagrams.py` using `reportlab.graphics.shapes.Drawing`, `Rect`, `Circle`, `Line`, `String`, `Polygon`, and `Path`. Define helpers with these signatures:

```python
def label(drawing, x, y, text, *, size=10, color=None, anchor="start") -> None: ...
def perfboard(drawing, x, y, width, height, *, copper_side=False) -> None: ...
def pad(drawing, x, y, *, soldered=False) -> None: ...
def wire(drawing, points, *, color, width=4, dashed=False) -> None: ...
def warning_mark(drawing, x, y, text) -> None: ...
def get_diagram(name: str): ...
```

Every diagram must label views as `부품면` or `납땜면`, show the bottom view horizontally mirrored where appropriate, and pair every colored wire with a text net label.

- [ ] **Step 4: Implement the fourteen diagrams**

Build diagrams that explicitly show:

- Board holder gripping only the perfboard edge, with the copper side facing upward for soldering.
- Iron tip touching both the copper pad and metal lead before solder is added.
- Correct volcano-shaped joint versus insufficient, oversized, cold, and bridged joints.
- The twentieth female-header socket being sacrificed while nineteen remain intact.
- ESP32 used only as an alignment jig while two header corner pins are tacked.
- Sensor pigtail entering from the component side while a bare tinned rail lies across the copper pads.
- Separate 5V, 3.3V, and GND rails with at least two empty pad rows between them.
- Both 10kΩ/20kΩ MQ dividers with GPIO34 and GPIO35 at their midpoints.
- Drive logic rails separate from the external motor-power path.

- [ ] **Step 5: Run diagram tests**

Run the full test script.

Expected: content and diagram tests pass.

- [ ] **Step 6: Commit the diagram library**

```powershell
git add tools\soldering_manual\diagrams.py tests\soldering_manual\test_manual.py
git commit -m "Add soldering manual diagrams"
```

---

### Task 3: Assemble the A4 PDF

**Files:**
- Create: `tools/soldering_manual/build_manual.py`
- Modify: `tests/soldering_manual/test_manual.py`
- Create: `docs/guides/HazardBot_만능기판_납땜_설명서.pdf`

**Interfaces:**
- Consumes: `content.SECTIONS`, `content.SENSOR_NETS`, `content.DRIVE_NETS`, and `diagrams.get_diagram()`.
- Produces: `build_manual(output_path: Path) -> Path` and a valid A4 PDF.

- [ ] **Step 1: Add a failing PDF smoke test**

Append a test that builds into a temporary directory, reads the output with `pypdf.PdfReader`, and checks the title, section text, and page count:

```python
import tempfile
from pypdf import PdfReader
from tools.soldering_manual.build_manual import build_manual

class ManualPdfTests(unittest.TestCase):
    def test_pdf_contains_both_boards_and_checklist(self):
        with tempfile.TemporaryDirectory() as temp_dir:
            output = Path(temp_dir) / "manual.pdf"
            build_manual(output)
            reader = PdfReader(str(output))
            self.assertGreaterEqual(len(reader.pages), 18)
            self.assertLessEqual(len(reader.pages), 26)
            text = "\n".join(page.extract_text() or "" for page in reader.pages)
            for phrase in ("센서용 기판", "주행용 기판", "GPIO34", "GPIO25", "통전 전 검사"):
                self.assertIn(phrase, text)
```

- [ ] **Step 2: Run tests and verify the builder import fails**

Run the full test script.

Expected: import failure for `tools.soldering_manual.build_manual`.

- [ ] **Step 3: Implement typography and page components**

Use A4 pages, 15mm margins, page numbers, and Korean fonts. Register `C:\Windows\Fonts\malgun.ttf` and `C:\Windows\Fonts\malgunbd.ttf`; fail with a clear message if either file is absent. Implement:

```python
def register_fonts() -> tuple[str, str]: ...
def build_styles() -> dict[str, ParagraphStyle]: ...
def step_block(number: int, title: str, body: str, diagram_name: str): ...
def warning_box(text: str): ...
def checkpoint(items: tuple[str, ...]): ...
def build_manual(output_path: Path) -> Path: ...
```

Do not place Korean text inside raster images; keep labels as vector text or PDF text for readability.

- [ ] **Step 4: Assemble the approved 18–22 page structure**

Build these page groups in order:

1. Cover and finished-board overview.
2. Safety, tools, board faces, and holder setup.
3. Four-step practice joint and good/bad comparison.
4. Header cutting, alignment, tack soldering, and full soldering.
5. Sensor-board placement, pigtail preparation, and three power rails.
6. Rail soldering sequence split into separate actions.
7. MQ dividers and all sensor signal wires.
8. Sensor-board inspection and V10 bring-up.
9. Drive-board placement, logic rail, TB6612 controls, and line sensor.
10. Motor-power boundary and wheel-off-ground bring-up.
11. Final inspection flow and one-page field checklist.

Use `PageBreak` deliberately so sensor and drive sections start on new pages.

- [ ] **Step 5: Run all automated tests**

Run:

```powershell
C:\Users\rkdgm\.cache\codex-runtimes\codex-primary-runtime\dependencies\python\python.exe tests\soldering_manual\test_manual.py
```

Expected: all tests pass and the temporary PDF has 18–26 pages.

- [ ] **Step 6: Build the final PDF**

Run:

```powershell
C:\Users\rkdgm\.cache\codex-runtimes\codex-primary-runtime\dependencies\python\python.exe tools\soldering_manual\build_manual.py --output docs\guides\HazardBot_만능기판_납땜_설명서.pdf
```

Expected: command prints the absolute PDF path and page count.

- [ ] **Step 7: Commit the PDF builder and first complete PDF**

```powershell
git add tools\soldering_manual\build_manual.py tests\soldering_manual\test_manual.py docs\guides\HazardBot_만능기판_납땜_설명서.pdf
git commit -m "Build illustrated soldering manual"
```

---

### Task 4: Render and Visually Verify Every Page

**Files:**
- Inspect: `docs/guides/HazardBot_만능기판_납땜_설명서.pdf`
- Create during QA: `tmp/soldering-manual-render/page-*.png`
- Modify if necessary: `tools/soldering_manual/content.py`
- Modify if necessary: `tools/soldering_manual/diagrams.py`
- Modify if necessary: `tools/soldering_manual/build_manual.py`
- Regenerate: `docs/guides/HazardBot_만능기판_납땜_설명서.pdf`

**Interfaces:**
- Consumes: final PDF from Task 3.
- Produces: visually approved PDF with no clipping, overlap, unreadable labels, or incorrect view mirroring.

- [ ] **Step 1: Render the PDF to page PNG files**

Use the PDF skill's bundled rendering command or Poppler at 150 DPI, writing all pages to `tmp/soldering-manual-render/`.

Expected: one PNG per PDF page.

- [ ] **Step 2: Create and inspect a contact sheet**

Create a contact sheet containing every page thumbnail and inspect overall rhythm, blank pages, section separation, and accidental overflow.

- [ ] **Step 3: Inspect critical pages at full resolution**

Inspect at least these pages individually:

- Board-holder orientation.
- Good/bad solder-joint comparison.
- Female-header cutting and ESP32 alignment.
- Rail cross-section and bottom-side mirroring.
- Sensor top/bottom layout and both MQ dividers.
- Drive top/bottom layout and motor-power boundary.
- Final one-page checklist.

- [ ] **Step 4: Correct every visual defect and rebuild**

Fix any clipped Korean text, overlapping labels, tiny callouts, incorrect left-right mirroring, page orphan, or ambiguous net. Rebuild the PDF and rerender all pages after the last change.

- [ ] **Step 5: Run final structural verification**

Run the full test script again and use `pypdf` or `pdfinfo` to confirm A4 page size and page count.

Expected: tests pass, all pages are A4, and every page has been visually inspected.

- [ ] **Step 6: Commit visual-QA corrections**

```powershell
git add tools\soldering_manual docs\guides\HazardBot_만능기판_납땜_설명서.pdf tests\soldering_manual\test_manual.py
git commit -m "Polish soldering manual layout"
```

---

### Task 5: Final Delivery Check

**Files:**
- Verify: `docs/guides/HazardBot_만능기판_납땜_설명서.pdf`
- Verify: `docs/superpowers/specs/2026-08-07-hazardbot-perfboard-soldering-manual-design.md`

**Interfaces:**
- Consumes: visually approved final PDF.
- Produces: final user handoff with an absolute clickable file link and concise usage note.

- [ ] **Step 1: Confirm the output exists and is non-empty**

Run a file listing that reports the absolute path, byte size, and modified time.

Expected: PDF exists under `docs/guides/` and has a non-zero size.

- [ ] **Step 2: Recheck the most safety-sensitive extracted text**

Extract the final PDF text and confirm it includes all of these phrases:

```text
교사 또는 성인의 감독
5V와 3.3V는 연결하지 않기
VM 12V는 로직 레일에 연결하지 않기
바퀴를 바닥에서 띄우기
이상하면 즉시 전원 분리
```

- [ ] **Step 3: Run the final test suite**

```powershell
C:\Users\rkdgm\.cache\codex-runtimes\codex-primary-runtime\dependencies\python\python.exe tests\soldering_manual\test_manual.py
```

Expected: exit code `0` with all tests passing.

- [ ] **Step 4: Deliver the PDF**

Provide a clickable absolute link to `docs/guides/HazardBot_만능기판_납땜_설명서.pdf`, state the verified page count, and advise reading the safety and practice sections before parts arrive.

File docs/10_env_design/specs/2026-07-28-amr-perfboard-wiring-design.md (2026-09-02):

# HazardBot AMR 시연용 만능기판 배선 설계

## 목적

세 명의 팀원이 반복 촬영하여 안정적인 시연 영상 한 편을 완성할 수 있도록, 제작 난도와 현장 수리성을 우선한 센서 배선 구조를 사용한다.

## 확정 구조

기능별 만능기판 2장 구조를 사용한다.

1. 메인 전원·인터페이스 기판
   - ESP32 #1 신호 연결
   - 5V, 3.3V, GND 분배
   - LiPo 전압분배 및 ADC 연결
   - Emergency Stop 입력
   - I2C와 개별 센서 커넥터 분배
2. 센서 분배 기판
   - 차체 전면 센서 케이블 집선
   - 센서별 잠금형 커넥터 제공
   - 고장 난 센서를 개별적으로 분리·교체

카메라는 Raspberry Pi 5에 USB 또는 CSI로 직접 연결한다. ESP32 #1과 Raspberry Pi 5의 핵심 통신은 USB 직렬 연결을 사용한다.

## 대상 센서

- MQ-2
- MQ-135
- VL53L1X
- TCS34725
- MLX90614
- KY-026
- FC-37
- 5채널 IR 라인트레이싱 모듈
- LiPo 전압 측정 입력
- Emergency Stop

ESP32 #2 ARM, STS3215, 그리퍼 및 출력 장치는 이 기판의 범위에서 제외한다.

## 연결 원칙

- 센서는 만능기판에 직접 납땜하지 않고 JST-XH 계열 잠금형 커넥터로 연결한다.
- I2C 센서 3종은 공통 SDA/SCL 버스를 사용하되 각각 분리 가능한 4핀 커넥터를 둔다.
- 아날로그 센서와 모터 전원 배선은 I2C 및 USB 케이블에서 떨어뜨린다.
- MQ 센서는 발열과 공기 흐름을 고려해 차체 상단에 별도 고정한다.
- 라인트레이싱 센서와 FC-37은 차체 하단에서 높이 조절이 가능해야 한다.
- 배터리 측정 회로는 배터리 사양 확정 후 구성한다. 프로젝트 안전 기준은 3S LiPo cutoff 9.9V를 유지한다.
- 모든 케이블에는 스트레인 릴리프와 라벨을 적용한다.

## 성공 기준

- 주행 진동 중 센서 커넥터가 빠지지 않는다.
- 센서 한 개를 전체 기판 탈거 없이 교체할 수 있다.
- ESP32와 RPi 5 사이 USB 직렬 통신이 촬영 동안 유지된다.
- Emergency Stop, 센서 오류, LiPo cutoff 및 통신 timeout이 안전 정지를 유지한다.
- 현장에서 납땜 수정 없이 예비 센서나 예비 케이블로 교체할 수 있다.

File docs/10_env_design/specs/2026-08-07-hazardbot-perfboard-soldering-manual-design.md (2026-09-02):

# HazardBot 만능기판 납땜 설명서 설계

## 목표

납땜 경험이 전혀 없는 초보자도 학교 실습실에서 교사 또는 성인의 감독 아래
HazardBot의 센서용 기판과 주행용 기판을 순서대로 제작할 수 있는 A4 PDF
설명서를 만든다. 설명서는 실제 부품 사진을 사실적으로 재현하는 것보다 기판의
방향, 점퍼선과 전원 레일의 위치, 고정대 사용법, 인두와 납을 대는 위치를 정확하게
보여주는 교육용 삽화를 우선한다.

최종 PDF는 한 파일이지만 센서용 기판과 주행용 기판을 명확하게 분리한다. 상세한
교과서형 설명과 작업대 옆에서 확인할 수 있는 요약 체크리스트를 함께 제공한다.

## 독자와 설명 원칙

- 대상 독자: 납땜을 한 번도 해보지 않은 초보자
- 목표 이해 수준: 12살이 읽어도 동작을 따라 할 수 있는 표현
- 한 단계에는 한 동작만 배치한다.
- 각 동작은 `지금 할 일 → 작업 전 상태 → 손과 도구 위치 → 실제 동작 → 성공한
  모습 → 흔한 실수 → 확인란` 순서로 설명한다.
- 전문 용어는 처음 등장할 때 쉬운 말과 함께 정의한다.
- 뜨거운 인두, 전원 인가, 모터 전원 작업은 교사 또는 성인의 감독 표시를 넣는다.
- 배선은 색만으로 구분하지 않고 핀 이름을 반복 표기한다.

## 결과물

- 형식: 인쇄 가능한 A4 PDF
- 예상 분량: 약 18~22페이지
- 구성: 표지, 공통 납땜 기초, 센서용 기판, 주행용 기판, 최종 검사 및 요약표
- 각 핵심 작업에는 위에서 본 배치, 아래에서 본 납땜면, 고정대에 끼운 옆모습,
  올바른 예와 잘못된 예를 포함한다.
- PDF 생성 후 모든 페이지를 이미지로 렌더링하여 잘림, 겹침, 작은 글자, 잘못된
  좌우 반전이 없는지 확인한다.

## 시각 체계

- 빨강: 5V 및 전원 양극
- 주황: 3.3V
- 검정: GND
- 파랑: 일반 센서 및 제어 신호
- 보라: MQ 센서 아날로그 신호와 분압회로
- 회색 점선: 연결하지 않는 핀
- 초록 테두리: 올바른 작업
- 빨강 테두리와 X: 잘못된 작업
- 손가락 표시: 잡아야 하는 부분
- 열 경고 표시: 인두 팁과 방금 납땜한 부분

실제 점퍼선 색이 다를 수 있으므로 모든 선에 `5V`, `3V3`, `GND`, `GPIO34`와
같은 기능 이름을 함께 표시한다.

## 문서 구성

### 1. 시작하기 전

- 완성할 두 기판의 역할
- 구매품과 기존 보유품
- 인두, 납, 고정대, 니퍼, 스트리퍼, 멀티미터의 역할
- 부품면과 구리면 구별
- 전원을 분리한 상태에서만 납땜해야 하는 이유
- 인두에서 잡아도 되는 부분과 만지면 안 되는 부분

### 2. 납땜 연습

- 실제 회로에서 떨어진 기판 모서리를 연습 구역으로 지정
- 인두 예열과 팁 주석 도금
- 구리 패드와 금속선을 동시에 데우는 방법
- 납 공급, 납 제거, 인두 제거의 순서
- 식는 동안 움직이지 않는 방법
- 정상 납땜, 납 부족, 납 과다, 냉땜, 인접 패드 합선 비교

### 3. 암헤더와 ESP32

- 20핀 암헤더의 끝 한 칸을 희생하여 19핀으로 만드는 방법
- 암헤더 두 줄을 ESP32에 먼저 꽂아 간격을 맞추는 방법
- USB 포트가 기판 밖을 향하도록 배치
- 대각선 모서리 핀만 먼저 납땜하고 수직을 확인한 뒤 나머지를 납땜
- 배선 작업 전 ESP32를 소켓에서 빼는 시점

### 4. 센서용 기판

- MQ-135, MQ-2, KY-026, VL53L1X의 단순화된 배치
- MQ 금속 망을 가리지 않고 VL53L1X 렌즈를 전방으로 향하게 하는 고정법
- 기존 암-암 점퍼선을 잘라 센서용 피그테일로 만드는 방법
- 5V, 3.3V, GND 레일의 위치와 필요한 접점 수
- 부품면에서 센서선을 먼저 구멍에 넣고 납땜면에 레일선을 놓는 순서
- 센서선, 구리 패드, 레일선을 한 납땜점에서 연결하는 방법
- MQ 센서 두 개의 10kΩ/20kΩ 분압회로
- 한 센서씩 연결하고 검사하는 방법
- V10 업로드 및 센서별 확인 순서

### 5. 주행용 기판

- 두 번째 ESP32 암헤더 장착
- TB6612FNG와 라인센서의 단순화된 배치
- TB6612FNG와 라인센서를 기존 점퍼선으로 연결하고 기판에 물리적으로 고정
- 3.3V 로직 레일과 로직 GND 레일
- 기존에 성공한 제어 핀 배선의 이전
- VM 12V, 전력 GND, A01/A02, B01/B02는 얇은 점퍼선이나 로직 레일을
  통과시키지 않고 기존 직접 연결을 유지
- USB와 로직 시험 후 바퀴를 띄우고 모터 전원을 연결하는 순서

### 6. 마지막 검사

- 모듈을 꽂기 전 육안 검사와 멀티미터 검사
- 5V-GND, 3.3V-GND 단락 확인
- 휴대폰 카메라 확대 검사
- 센서 기판과 주행 기판의 분리 시험
- 촬영 직전 한 장 체크리스트

## 센서 기판 배선 정본

### 전원

| 레일 | 소스 | 연결 대상 |
|---|---|---|
| 5V | ESP32 5V/VIN | MQ-135 VCC, MQ-2 VCC |
| 3.3V | ESP32 3V3 | KY-026 VCC, VL53L1X VIN |
| GND | ESP32 GND | 센서 4개 GND, 두 20kΩ 저항의 GND 쪽 |

### 신호

| 센서 | 연결 |
|---|---|
| MQ-135 AO | 10kΩ → 분압 중점 → GPIO34 |
| MQ-135 분압 중점 | 20kΩ → GND |
| MQ-2 AO | 10kΩ → 분압 중점 → GPIO35 |
| MQ-2 분압 중점 | 20kΩ → GND |
| KY-026 DO | GPIO27 |
| VL53L1X SDA | GPIO21 |
| VL53L1X SCL | GPIO22 |

MQ 센서 DO, KY-026 AO, VL53L1X INT와 XSHUT은 연결하지 않는다.

## 주행 기판 배선 정본

### TB6612FNG 로직

| TB6612FNG | ESP32 |
|---|---|
| PWMA | GPIO25 |
| AIN1 | GPIO26 |
| AIN2 | GPIO27 |
| PWMB | GPIO14 |
| BIN1 | GPIO16/RX2 |
| BIN2 | GPIO17/TX2 |
| STBY | GPIO4 |
| VCC | 3.3V |
| 로직 GND | GND |

### 라인센서

| 라인센서 | ESP32 |
|---|---|
| VCC | 3.3V |
| GND | GND |
| S1 | GPIO13 |
| S2 | GPIO18 |
| S3 | GPIO19 |
| S4 | GPIO23 |
| S5 | GPIO32 |

TB6612FNG의 VM 12V, 전력 쪽 GND, A01/A02, B01/B02는 만능기판의 얇은
점퍼선과 로직 전원 레일에 넣지 않는다. 기존에 시험한 직접 연결을 유지하고
설명서에는 `이번 납땜 작업에서 변경하지 않음`으로 표시한다.

## 부품 사용 범위

- 단면 100×100mm, 2.54mm 만능기판 2개
- 20핀 2.54mm 암헤더 4개를 각각 19핀으로 가공하여 두 ESP32에만 사용
- TB6612FNG와 센서 모듈은 소켓을 추가하지 않고 기존 점퍼선을 사용
- 보유 중인 10kΩ, 20kΩ 저항 사용
- 보유 중인 점퍼선을 센서 및 로직 배선과 전원 레일 재료로 재사용

## 작업 순서와 검사 정책

1. 전원과 모든 모듈을 분리한다.
2. 빈 기판에서 납땜 연습을 한다.
3. ESP32를 정렬 지그로 사용해 암헤더 모서리만 먼저 납땜한다.
4. 수직을 확인한 후 헤더의 나머지 핀을 납땜한다.
5. ESP32를 빼고 센서선과 로직선을 배치한다.
6. 부품면에서 선을 먼저 넣고 납땜면에서 공통 레일을 놓아 함께 납땜한다.
7. 한 연결을 만들 때마다 육안으로 확인하고, 한 기능 블록이 끝날 때마다
   멀티미터로 도통과 단락을 검사한다.
8. 모듈을 모두 빼고 최종 단락 검사를 한다.
9. ESP32만 꽂아 USB 전원으로 부팅을 확인한다.
10. 센서 기판은 센서를 하나씩 추가한다.
11. 주행 기판은 로직을 먼저 확인하고 마지막에 바퀴를 띄운 상태로 기존 모터
    전원을 연결한다.

## 완료 기준

- PDF에서 센서용 기판과 주행용 기판이 제목, 색상, 페이지 구성으로 명확히
  분리되어 있다.
- 초보자가 기판의 부품면과 납땜면, 고정대 방향, 인두와 납의 위치를 그림만 보고
  구별할 수 있다.
- 센서 및 주행 핀 배선표가 프로젝트의 확정값과 일치한다.
- 5V, 3.3V, GND, 12V 모터 전원이 서로 혼동되지 않는다.
- 실제 보유품 외에 새로운 부품을 필수로 요구하지 않는다.
- 모든 페이지를 렌더링해 내용 잘림, 그림 겹침, 좌우 반전 오류가 없음을 확인한다.

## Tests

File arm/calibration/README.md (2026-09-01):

# 캘리브레이션 백업

LeRobot 캘리브레이션 파일의 백업본. **이 파일을 잃으면 재캘리브레이션이 필요하고,
데이터 수집 이후에 재캘리브레이션하면 기존 데이터셋이 무효가 된다.**

## 파일

| 파일 | 대상 | 생성일 |
|---|---|---|
| `follower_arm.json` | 팔로워암 (SO-ARM101, STS3215 ×6) | 2026-07-10 |
| `leader_arm.json` | 리더암 (SO-ARM101, STS3215 ×6, 7.4V) | 2026-07-11 |

## 원본 위치 — **리더와 팔로워의 경로가 다르다**

```
팔로워: %USERPROFILE%\.cache\huggingface\lerobot\calibration\robots\so_follower\follower_arm.json
리더:   %USERPROFILE%\.cache\huggingface\lerobot\calibration\teleoperators\so_leader\leader_arm.json
```

팔로워는 **robot**, 리더는 **teleoperator** 로 분류되어 `robots/` 와 `teleoperators/` 로 갈린다.
디렉터리 이름도 `so_follower` / `so_leader` 다 (`so101_*` 이 아니다 — 그건 등록된 별칭이고
실제 클래스 이름이 경로가 된다).

LeRobot 명령은 `--robot.id=follower_arm` / `--teleop.id=leader_arm` 으로 파일을 찾는다.
**id 이름이 곧 파일명이다.**

## 복원 방법

```powershell
$base = "$env:USERPROFILE\.cache\huggingface\lerobot\calibration"

$dst = "$base\robots\so_follower"
New-Item -ItemType Directory -Force -Path $dst | Out-Null
Copy-Item ".\follower_arm.json" -Destination $dst -Force

$dst = "$base\teleoperators\so_leader"
New-Item -ItemType Directory -Force -Path $dst | Out-Null
Copy-Item ".\leader_arm.json" -Destination $dst -Force
```

## 왜 백업하는가

캘리브레이션 값은 **두 곳에** 저장된다.

| 데이터 | 저장 위치 | 비고 |
|---|---|---|
| 서보 ID, homing_offset, min/max 한계 | **서보 내부 EPROM** | 비휘발성 — 전원을 빼도 유지됨 |
| 동일한 값의 사본 | **PC의 이 JSON 파일** | LeRobot이 실행 시 참조 |

서보에 값이 남아 있어도 **LeRobot은 PC의 JSON을 찾는다.** 파일이 없으면 재캘리브레이션해야 한다.

그리고 **ACT 정책은 캘리브레이션된 좌표계에서 학습된다.** 데이터 수집 후 영점이 바뀌면
같은 숫자가 다른 물리 자세를 가리키게 되어 **데이터셋을 통째로 버려야 한다.**

→ **수집 시점과 배포 시점의 캘리브레이션은 반드시 동일해야 한다.**

## ⚠️ 주의

- **`lerobot-setup-motors` 를 다시 실행하지 말 것.** ID 부여 과정에서 서보 EPROM 설정이
  초기화될 수 있다. 팔로워는 ID 부여가 이미 끝났으므로 재실행할 이유가 없다.
- 캘리브레이션을 다시 하면 **이 백업도 함께 갱신할 것.**

## 현재 값 (2026-07-10, follower_arm)

| 축 | ID | homing_offset | range_min | range_max |
|---|---|---|---|---|
| shoulder_pan | 1 | 1672 | 1151 | 3856 |
| shoulder_lift | 2 | -1563 | 1462 | 3746 |
| elbow_flex | 3 | 1496 | 804 | 3021 |
| wrist_flex | 4 | 1999 | 919 | 3242 |
| wrist_roll | 5 | **-1968** | **260** | **3836** | ← 2026-08-20 카메라 장착 후 재갱신 |
| gripper | 6 | -1510 | 1313 | 2793 |

나머지 축은 모두 `range_min < 2048 < range_max` 이고 0/4095 에 닿지 않는다 — 합격 기준을 만족한다.

`wrist_roll` 은 원래 0~4095(연속 회전축 기본값)였으나 배선 보호를 위해 창을 제한했다.
**손목 카메라 장착(2026-08-20) 후 재측정한 현재 창은 ±157°(총 314°)** 이고, 창 중심은
정렬 영점이 아니라 **기본위치(영점 −44°, `follower_home.json` = present 2048)** 다 —
시작 자세에서 양방향 대칭 ±157° 가 나오도록 잡았다. 정렬 영점은 present **2544**.
실측 한계는 영점 기준 팔로워 −210°/+126°, 리더 −214°/+122° 이고 여유 100카운트를 뺀
교집합 전체가 창이다. 전 구간 정착 부하 ≤48(한계의 5%), 창 끝단 추종 오차 ≤8카운트,
텔레옵 60초 무결 확인(2026-07-16). 자세한 경위는 구축기록 §5-8.

## 현재 값 (2026-07-11, leader_arm)

| 축 | ID | homing_offset | range_min | range_max | 범위 | 팔로워 대비 |
|---|---|---|---|---|---|---|
| shoulder_pan | 1 | -1402 | 776 | 3439 | 234.1° | 238° |
| shoulder_lift | 2 | **-1061** | 991 | 3219 | 195.8° | 201° |
| elbow_flex | 3 | 285 | 629 | 2816 | 192.2° | 195° |
| wrist_flex | 4 | 1167 | 762 | 3077 | 203.5° | 204° |
| wrist_roll | 5 | **1057** | **260** | **3836** | 314.3° | 314.3° (동일) | ← 2026-08-20 카메라 장착 후 재갱신 |
| gripper | 6 | 31 | 2037 | 3307 | 111.6° | 130° |

> `wrist_roll` 은 양팔이 **같은 창 폭·같은 영점 상대위치**를 써야 1:1 대응이 된다.
> 한쪽만 바꾸면 손목 방향이 어긋난다 — 반드시 `widen_wrist_roll.py` 로 양팔을 함께 갱신할 것.
>
> 🔴 정렬 영점은 `wrist_zero.json` 에 **원시 엔코더 값**으로 보관한다 (팔로워 576 / 리더 3601).
> 창이나 `Homing_Offset` 을 바꿔도 이 값은 건드리지 않는다 — 서보 혼을 분해했을 때만 갱신한다.

전 축이 팔로워 실측치와 일치한다. `gripper` 만 `range_min` 이 2047 에 10 카운트 차로 붙어 있는데,
정규화는 `range_min~range_max` 를 기준으로 하므로 동작에는 문제가 없다.

### 🔴 shoulder_lift 의 homing_offset 은 자동 계산값이 아니다

이 축은 **가동 범위가 원시 엔코더 0 을 가로질러** 훑는 도중 값이 감겼다(wrap).
`lerobot-calibrate` 의 `set_half_turn_homings()` 로는 해결되지 않는다.

Feetech 서보가 `Homing_Offset` 을 **감김 이전에** 적용한다는 점을 이용해,
감김 지점을 관절이 지나가지 않는 구간으로 밀어 해결했다. `Homing_Offset` 은
부호+크기 12비트라 **±2047 이 한계**이므로 필요한 값 3035 대신 **모듈로 등가인 -1061** 을 썼다.

→ **재캘리브레이션 시 `tools/calibrate_leader.py --step homing --skip shoulder_lift` 를 쓸 것.**
   `lerobot-calibrate` 를 그냥 돌리면 이 값이 덮어써져 래핑이 재발한다.

## 도구

| 파일 | 용도 |
|---|---|
| `tools/check_leader.py` | 리더 통신·전압 검증 (7.4V 기준. `check_follower.py` 는 12V 기준이라 오검출) |
| `tools/set_leader_id.py` | 서보 ID 를 한 번에 하나씩 부여 |
| `tools/calibrate_leader.py` | 캘리브레이션 단계 분리 (`raw`→`aim`→`homing`→`ranges`) |
| `tools/measure_leader_range.py` | 가동 범위만 측정 |

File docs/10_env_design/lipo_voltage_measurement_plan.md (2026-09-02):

# 3S LiPo 전압 측정 설계 메모

## 목적

ESP32 #1 AMR v7은 3S LiPo cutoff 기준을 `9.9V`로 유지해야 한다. 현재 펌웨어에는 `LIPO_CUTOFF_VOLTAGE = 9.9` 조건이 있지만, 실제 전압은 `currentBatteryVoltage = 12.0` 임시값으로 고정되어 있다. 따라서 실제 배터리 보호 기능을 완성하려면 ESP32 ADC로 LiPo 전압을 측정하는 회로와 변환식이 필요하다.

## 모터와의 관계

LiPo 전압 측정은 모터를 직접 제어하는 기능은 아니다. 하지만 AMR 안전에는 강하게 연결된다.

- 모터가 큰 전류를 쓰면 배터리 전압이 순간적으로 떨어질 수 있다.
- 배터리 전압이 낮은 상태에서 계속 주행하면 LiPo 과방전 위험이 있다.
- 전압이 낮아지면 ESP32, 센서, 모터 드라이버가 불안정해질 수 있다.
- 따라서 전압이 `9.9V` 이하이면 상태 평가에서 `STOP`으로 전환하고, action은 `STOP_MOTION`이 되어야 한다.

즉, LiPo 측정은 “모터를 움직이기 위한 기능”이 아니라 “모터를 멈춰야 할 때를 판단하는 안전 입력”이다.

## 왜 전압 분배가 필요한가

3S LiPo는 완충 시 약 `12.6V`까지 올라간다. ESP32 ADC 입력은 보통 3.3V 범위를 넘기면 안 된다. 그래서 배터리 전압을 저항 2개로 낮춰 ADC 핀에 넣어야 한다.

기본 회로:

```text
LiPo + ---- R1 ----+---- ADC_PIN
                  |
                  R2
                  |
LiPo - -----------+---- GND
```

계산식:

```text
Vadc = Vbat * R2 / (R1 + R2)
Vbat = Vadc * (R1 + R2) / R2
```

예를 들어 `R1 = 100kΩ`, `R2 = 33kΩ`이면:

```text
분배비 = 33 / (100 + 33) = 0.248
12.6V * 0.248 = 약 3.12V
```

이 값은 ESP32 ADC 입력 범위 안에 들어온다.

## 코드에 들어갈 구조

실제 구현 시에는 다음 상수를 둔다.

```cpp
const int LIPO_ADC_PIN = 35;
const float LIPO_R1_OHMS = 100000.0;
const float LIPO_R2_OHMS = 33000.0;
const float ADC_REFERENCE_VOLTAGE = 3.3;
const int ADC_MAX_VALUE = 4095;
```

그리고 다음 함수로 분리한다.

```cpp
float readBatteryVoltage();
```

이 함수는 ADC raw 값을 읽고, ADC 전압으로 바꾼 뒤, 전압 분배 역산으로 실제 LiPo 전압을 계산한다.

개념식:

```cpp
float adcVoltage = raw * ADC_REFERENCE_VOLTAGE / ADC_MAX_VALUE;
float batteryVoltage = adcVoltage * (LIPO_R1_OHMS + LIPO_R2_OHMS) / LIPO_R2_OHMS;
```

## v7 상태 평가와 연결

현재 v7의 상태 평가 우선순위는 다음 흐름을 유지한다.

1. Emergency Stop이면 `STOP`
2. LiPo 전압이 `9.9V` 이하이면 `STOP`
3. 센서 오류이면 `SENSOR_ERROR`
4. RPi timeout이면 `STOP`
5. DANGER/WARNING/SAFE 판단

LiPo 측정 구현 후에는 `currentBatteryVoltage = 12.0` 고정값 대신 `readBatteryVoltage()` 결과를 사용한다.

## 실제 구현 전 확인할 것

아직 바로 코드를 바꾸기 전에 다음 값을 확정해야 한다.

- LiPo 전압 측정에 사용할 ESP32 ADC 핀
- 전압 분배 저항값 `R1`, `R2`
- 사용하는 ESP32 보드의 ADC 입력 허용 범위
- GND가 LiPo, ESP32, 모터 드라이버 사이에서 공통으로 연결되는지
- 멀티미터로 측정한 실제 배터리 전압과 ADC 계산값의 오차

## 테스트 방법

하드웨어 없이 가능한 테스트:

- Python 하네스에서 raw ADC 값 -> 배터리 전압 변환식을 검증한다.
- `9.9V` 이하일 때 `STOP`으로 평가되는지 확인한다.

실제 보드에서 필요한 테스트:

- 멀티미터로 LiPo 전압을 측정한다.
- ESP32가 계산한 `BAT=` 값과 비교한다.
- 배터리 전압이 낮은 상황을 전원공급기나 안전한 테스트 회로로 재현한다.
- `BAT <= 9.9V`일 때 `STATE=STOP`으로 전환되는지 확인한다.

## 주의사항

- LiPo를 ESP32 ADC 핀에 직접 연결하면 안 된다.
- 전압 분배 회로 없이 12V대 전압을 ADC에 넣으면 보드가 손상될 수 있다.
- 모터 부하로 순간 전압 강하가 생길 수 있으므로, 나중에 평균 필터나 최소 지속 시간 조건을 검토할 수 있다.
- cutoff 기준 `9.9V`는 3S 기준 셀당 약 `3.3V`이다.

## 추천 다음 단계

1. 실제 사용할 ADC 핀을 정한다.
2. 전압 분배 저항값을 정한다. 시작안은 `R1 = 100kΩ`, `R2 = 33kΩ`이다.
3. Python 하네스에 ADC 변환식 테스트를 추가한다.
4. Arduino v7에 `readBatteryVoltage()`를 추가한다.
5. 실제 보드에서 멀티미터 값과 `BAT=` 출력값을 비교해 보정한다.

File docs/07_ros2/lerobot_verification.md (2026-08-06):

# LeRobot 배포 검증 기록

- `~/lerobot-venv`에 격리 venv 설치 (`--system-site-packages` 미사용,
  ROS2의 opencv/cv_bridge와 충돌 방지 목적)
- `python rpi_check.py --skip-cameras` : 읽기 전용 테스트 전항목 통과
- `python rpi_check.py --skip-cameras --move-all` : 6축 실제 구동 확인
- arm_controller는 서보 버스를 직접 건드리지 않으므로 검증 중 ROS2 스택은
  계속 실행 상태로 두어도 무방 (단, arm_controller는 이 검증 동안 미실행)

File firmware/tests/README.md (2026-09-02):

# ENV 보드 로직 테스트

`firmware/esp32_env/` 스케치의 상태 판정 로직을 **하드웨어 없이** 검증한다.
`.ino` 를 그대로 돌릴 수는 없으므로, 각 테스트는 스케치의 상태머신을 파이썬으로
재구현해 두고(`*_pure.py`) 두 가지를 함께 확인한다.

1. 재구현한 상태머신이 설계대로 동작하는가 (전이·임계·폴백)
2. **실제 `.ino` 원본이 그 계약을 여전히 지키고 있는가** — 소스를 읽어
   필수 상수·함수가 있는지, 폐기된 센서 계약이 남아 있지 않은지 대조한다

즉 스케치를 고치고 테스트를 안 고치면 `T_SRC_*` 항목이 깨진다.

## 실행

`amr_v8` · `amr_v9` 는 자체 러너를 쓰므로 파일을 직접 실행한다.

```bash
python -m unittest discover -s firmware/tests/amr_v7 -t firmware/tests/amr_v7   # 14건
python firmware/tests/amr_v8/test_amr_v8_pure.py                                # 22건
python firmware/tests/amr_v9/test_amr_v9_pure.py                                # 21건
```

2026-09-03 기준 57건 전부 통과한다.

## 무엇을 보는가

| 폴더 | 대상 | 핵심 검증 |
| --- | --- | --- |
| `amr_v7/` | 폐기된 v7 상태머신 + RPi 측 도구 2종 | 체크섬 계산 · keepalive 타임아웃 |
| `amr_v8/` | 폐기된 v8 | RPi 타임아웃 시 STOP 폴백 · DANGER 연속 검출 요건 |
| `amr_v9/` | `firmware/esp32_env/AMR_state_v9_ino/` | 3센서 계약 · **미납땜 거리센서가 빠졌는지** |

v7·v8 스케치 원본은 [`archive/firmware_esp32_env_history/`](../../archive/firmware_esp32_env_history/) 에 있다.

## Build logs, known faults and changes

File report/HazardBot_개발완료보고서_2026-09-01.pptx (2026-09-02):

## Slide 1

제24회 임베디드SW경진대회 개발완료보고서

HazardBot

자유공모 부문

위험물 취급구역을 순찰하며 감지·판정하고, 로봇팔로 직접 제거하는 AI 패트롤 로봇

확정 후 삽입

2026-09-03

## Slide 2

00 · 목차

목차

대회 필수항목 7개에 맞춘 5개 장 · 본문 20페이지

개발 개요
개발 배경·동기 · 목표·필요성 · 작품 개요와 제출 링크

개발 환경
시스템 개요 · 하드웨어와 전력 계통 · 개발 환경과 오픈소스 · 소프트웨어 아키텍처 · 파일 구성

개발 프로그램
위험물 판정 로직 · GAS_CHECK · ACT 학습 · ACT 초동 조치 · 통합 파이프라인과 대시보드 · 검증 결과

장애요인과 해결
개발 중 발생한 문제와 해결 방안

결과와 일정
작품의 차별성 · 기술적 우수성 · 파급력과 기대효과 · 개발 일정과 업무 분장

HazardBot 개발완료보고서

01

02 – 04

02

05 – 09

03

10 – 15

04

16

05

17 – 20

01 / 20

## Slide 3

01 · 개발 개요

사람이 계속 지킬 수 없는 구역이 있다

24시간 가동하는 위험물 취급구역에서, 감시와 초동 조치는 여전히 사람의 몫으로 남아 있다

24시간 가동 현장

위험물 상시 취급

사람의 지속 감시

접근 · 조치 지연

자동 감지 · 초동 조치

현장 조건

지속 감시의 한계

반도체 FAB·정유공장처럼 위험물을 다루면서도 멈추지 않는 현장이 있다. 사람이 밤낮없이 모든 구간을 같은 집중으로 지키는 것은 현실적으로 어렵다.

HazardBot 개발완료보고서

작업자 위험

근접이 곧 위험

위험물을 치우려면 사람이 유해 물질에 직접 다가가야 한다. 조치를 하는 행위 자체가 작업자에게 새로운 노출을 만든다.

개발 동기

발견 다음이 비어 있다

기존 순찰 로봇은 발견하고 알리는 데서 멈춘다. 치우는 일은 여전히 사람 몫으로 남아, 발견에서 조치까지의 간격이 사고 규모를 가른다.

02 / 20

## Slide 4

01 · 개발 개요

감지 · 판정 · 초동 조치를 하나의 흐름으로

사람이 직접 접근하지 않고도 위험물을 감지·판정하고, 제거까지 수행하는 로봇을 만든다

순찰 경로와 정지 지점을 구성한 시연 공간
바닥의 검은 선이 순찰 경로, 회색 패널이 각 정지 지점이다. 지점마다 판정 대상 물체와 격리함을 배치했다.

01
자동 감지
순찰 중 정지 지점마다 카메라로 물체를 확인한다


02
규칙 기반 판정
색상으로 1차 분류하고, 필요한 경우에만 가스 센서로 정밀검사한다

03
초동 조치
위험으로 판정되면 로봇팔이 직접 집어 격리함에 넣는다

설계 근거 — 위험물안전관리법 유별 혼재 제한 · KS C IEC 60079-10-1

HazardBot 개발완료보고서

03 / 20

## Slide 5

01 · 개발 개요

작품 개요와 제출 링크

대회 가이드양식의 개발 개요 표를 그대로 채웠다 — 소스코드와 시연동영상 링크는 필수 항목이다

HazardBot

위험물을 다루면서도 24시간 멈추지 않는 산업현장에서, 감시와 초동 조치는 여전히 사람의 몫으로 남아 있다.

기존 순찰 로봇은 발견하고 알리는 데서 멈춘다. 발견 이후 치우는 일은 사람이 위험물에 직접 다가가야 한다.

위험물을 자동으로 감지·판정하고, 판정 결과에 따라 로봇팔로 초동 조치(제거)까지 수행하는 로봇을 개발한다.

사람이 직접 접근하지 않고도 지속적인 감시·격리가 가능한 구조를 만들어, 유해물질에 근접하는 횟수 자체를 줄인다.

HazardBot 개발완료보고서

소스코드 링크

확정 후 삽입

github.com/<사용자이름>/2026ESWContest_free_<팀명>

작품명

GitHub

개발 배경

동기

목표

시연 동영상 링크

확정 후 삽입

2026ESWContest_자유공모_<팀명>_시연동영상 · 3분 이내 · 720p 이상

04 / 20

YouTube

필요성

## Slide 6

02 · 개발 환경

HazardBot — 감지에서 초동 조치까지

위험물 취급구역을 순찰하며 정지 지점마다 감지·판정하고, 로봇팔로 직접 제거한다

하드웨어 구성

RPi 5
ROS2 오케스트레이션 · 카메라 인식

ESP_Drive
TB6612FNG 모터 드라이버 · 안전 우선순위

ESP_Env
MQ-2 가스 · 화염 센서 3초 샘플링

SO-101 로봇팔
ACT 정책 · RTX 4060 GPU 추론

01 감지

02 판정

황색 — 산화성 고체
취급구역 내 위치 자체가 위반

03 표시 · 조치

대시보드 실시간 표시
상태 · 센서 수치 · 판정 문장 로그

카메라 인식
정지 지점마다 물체 색 확인

즉시 위험

적색 — 인화성 액체
MQ-2 가스 3초 정밀검사

로봇팔 초동 조치
파지 → 이동 → 격리함 → 뚜껑 닫기

검출 → 위험

없음 → 통과

ACT 파지 성공률

86.7%

실물 30회 검증 · 근거리 100%

가스 정밀검사

3초

MQ-2 샘플링 · 5초 워치독

ACT 학습 데이터

100회

리더암 직접 시연 · 모방학습

판정 로직 실물 확인

7회

3케이스 전부 정상 동작

05 / 20

HazardBot 개발완료보고서

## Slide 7

02 · 개발 환경

네 개의 하드웨어 단위와 세 개의 전력 레일

RPi 5가 전체 흐름을 조율하고 두 개의 ESP32와 로봇팔이 주행·센싱·조치를 맡는다 — 전원은 배터리 하나에서 세 갈래로 나뉜다

전력 계통 — 3S LiPo 11.1V · 2200mAh 에서 세 개 레일로

MQ-2 는 히터가 상시 330mA를 끌어 DRIVE 5V 를 흔들기 때문에 ESP_Env 5V/VIN 에서 따로 급전한다 · ESP 보드 전원선은 진동 이탈을 막으려 VCC/GND 직납땜 (16p)

오케스트레이션

RPi 5

ROS2 노드 조율
판정부터 조치까지 관리

카메라 물체 인식
색상 · 방위각 산출

대시보드 웹서버
hazardbot.local:8080

주행 · 안전 판단

ESP_Drive

TB6612FNG
듀얼 H-브리지 모터 제어

안전 우선순위 판단
위험 순위대로 정지 처리

라인 · 거리 센싱
TCRT5000 · VL53L1X

가스 · 화염 센싱

ESP_Env

MQ-2 가스센서
원시값 샘플링 · 화염 병행

3초 정밀검사
요청 시 집중 샘플링

판정 결과 전달
DETECTED · CLEAR · ERROR

초동 조치

SO-101 로봇팔

리더 - 팔로워 구조
시연을 관절값으로 수집

ACT 정책 제어
학습된 정책으로 파지

노트북 GPU 추론
RTX 4060 · COM3 직결

3S LiPo 배터리
11.1V · 2200mAh

XT60 1to3

로봇팔 서보 6개 전용

12V — 팔로워

SO-101 팔로워 암 · 6축

RPi 5 전용 레일

5V_RPi — XL4016 단독

주행 및 센서 계통

12V 주행 + 5V_ESP — XL4015

RPi 5 · ROS2 · 카메라 · 대시보드

TB6612 · ESP_Drive · ESP_Env

06 / 20

HazardBot 개발완료보고서

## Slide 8

02 · 개발 환경

개발 환경과 활용한 오픈소스

규정 제10조 ③에 따라, 기존 소프트웨어의 출처와 우리가 바꾸거나 더한 것을 함께 밝힌다

개발 환경

활용한 오픈소스 — 출처 · 라이선스 · 우리가 바꾸거나 더한 것

개선점 · 추가한 것

미션 통합 레이어로 자체 패키지 8종을 새로 작성했다.

표준 record 는 에피소드 사이 리더암 조작을 요구해 무인 롤아웃이 안 된다. 「에피소드 1회 = 프로세스 1회」 패치 러너로 재구성하고, HuggingFace 자동 업로드 기본값을 차단했다.

파지 → 격리함 투입 → 뚜껑 닫기를 단일 에피소드 태스크로 재정의해 100 에피소드를 자체 수집·학습했다.

원본이 테이블 클램프 설계라 2WD 섀시 어댑터를 v2까지 자체 모델링했고, 표준 캘리브레이션이 못 잡는 축을 위해 전용 도구를 직접 만들었다.

실시간 판정 대시보드를 새로 구현했다.

본 보고서 서체는 Pretendard (SIL OFL 1.1), 이미지는 전부 자체 촬영·자체 제작이다.

중앙 제어기

Raspberry Pi 5 · Ubuntu 24.04 LTS
ROS 2 Jazzy · Python 3.12 (rclpy)

학습 · 추론

Windows 11 노트북 · RTX 4060 (8GB)
miniconda 환경 lerobot · Python 3.10

로봇팔 스택

비전

LeRobot 0.4.4 · PyTorch (CUDA)
SCServo 라이브러리 · CP210x USB 시리얼

libcamera · OpenCV · cv_bridge
정지 지점 색상 · 방위각 산출

임베디드

대시보드

ESP32 × 2 · Arduino 스케치(.ino)
OTA 업로드 · TB6612FNG · MQ-2 · VL53L1X

Flask · Flask-SocketIO
RPi 호스팅 · hazardbot.local:8080

형상관리 · CI

GitHub · GitHub Actions 2종
Arduino 컴파일 / colcon build (Jazzy)

3D 제작

STEP · STL · 3mf 자체 모델링
PLA 출력 — 섀시 어댑터 · 카메라 프레임

오픈소스

ROS 2 Jazzy

라이선스

Apache-2.0

LeRobot 0.4.4

ACT (Action Chunking Transformer)

Apache-2.0

논문 구현

SO-ARM101 · lerobot-calibrate

Apache-2.0

Flask · Flask-SocketIO · OpenCV

BSD · Apache-2.0

HazardBot 개발완료보고서

07 / 20

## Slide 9

02 · 개발 환경

ROS2 노드가 판정과 조치를 이어 붙인다

인식 · 센싱 · 주행 노드가 판정 노드로 모이고, 오케스트레이터가 표시와 조치로 내보낸다

hazard_detector_node
색상 1차 분류 + 가스 결과로 위험 판정

mission_orchestrator
판정 결과에 따라 조치를 요청하고 상태를 관리

HazardBot 개발완료보고서

판정 계통 토픽

/vision/detected
인식한 물체의 색상 · 방위각

/hazard/gas_check_request
적색일 때 가스 정밀검사 요청

/env/gas_result
DETECTED · CLEAR · ERROR

/hazard/detected
최종 위험 판정과 판정 문장

vision_node
카메라 물체 인식

/vision/detected

sensor_bridge_node
ENV 보드 중계

/env/gas_result

amr_bridge_node
DRIVE 보드 중계

/amr/object_near

/hazard/detected

조치 · 상태 계통 토픽

/amr/object_near
정지 지점에서 물체 근접 감지

/amr/stop_index
현재 정지 지점 번호

/arm/grip_request
로봇팔 초동 조치 요청

/arm/act_result
정책 실행 결과 회신

08 / 20

판정 · 상태 갱신

/arm/grip_request

/arm/act_result

dashboard_node
실시간 판정 화면

arm_act_node
ACT 정책 실행

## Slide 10

02 · 개발 환경

파일 구성 · 주요 함수

저장소를 열었을 때 어디에 무엇이 있고, 어느 함수가 앞의 주장을 떠받치는지

저장소 구조

HazardBot 개발완료보고서

앞 장의 주장을 떠받치는 함수

analyze_frame() · vision_node
HSV 마스크에서 가장 큰 윤곽을 잡아 minAreaRect 로 색과 방위각을 낸다. 10p 판정의 입력이 여기서 나온다.

vision_cb() · hazard_detector
황색이면 그 자리에서 위험으로 판정하고, 적색이면 ENV 에 가스 검사를 요청한다. 10p 규칙이 곧 이 함수다.

updateGasInspection() · ENV 헤더
3초를 채우기 전에는 결과를 내지 않는 게이트(11p). constexpr 순수 함수라 하드웨어 없이 시험할 수 있다.

pollToF() · esp32_drive_tcp
장애물 300mm 가 3회 연속이면 doStop() 을 직접 부른다. RPi 를 거치지 않는 정지 경로다.

transition() · mission_orchestrator
IDLE → PATROL → … → REPORT 상태 전이가 지나는 단 하나의 창구. 상태 변경이 여러 곳에 흩어지지 않는다.

grip_request_cb() · arm_act_node
판정을 받아 ACT 롤아웃을 띄우고 결과를 되돌려준다. 14p 파이프라인의 이음매다.

verify_checksum() · 브리지 3종
ASCII 합 % 256 을 못 맞춘 프레임은 버린다. 두 ESP32 와 RPi 가 같은 규칙을 쓴다.

09 / 20

HazardBot/

├ ros2_ws/src/

├ firmware/

ROS2 패키지 9종 · RPi 5

│ ├ esp32_drive/

│ ├ esp32_env/

│ ├ tools/

DRIVE 스케치 6종

ENV 스케치 · 판정 헤더

ENV 프로토콜 파서

│ └ tests/

├ arm/

로직 테스트 57건

│ ├ tools/

│ ├ act/

│ ├ scripts/

STS3215 제어 · 진단 17종

ACT 수집 · 검수 · 데이터셋 메타

teleop · record · rollout

│ └ calibration/

├ docs/

캘리브레이션 정본 4개

설계 · 일정 · 실배선 기록 71건

├ hardware/

├ report/

출력에 쓴 STL 3종

이 보고서 빌드 시스템

└ archive/

폐기 설계 · ENV v1~v8

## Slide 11

03 · 개발 프로그램

색으로 나누고, 필요할 때만 가스로 확인한다

고체는 놓여 있는 것만으로 위반, 액체는 새어 나올 때만 위험 — 물질의 성질을 규칙으로 옮겼다

정지 지점 도착
순찰 중 지정된 지점에 정지

카메라 색상 확인
물체의 색과 방위각을 산출

색상별 규칙 적용
황색은 즉시, 적색은 가스 검사

판정 문장 출력
대시보드에 결과를 그대로 표시

황색 산화성 고체

황색 산화성 고체 감지 — 취급구역 내 위치 자체가 위반

고체는 가스를 내뿜지 않는다. 그 자리에 있다는 사실만으로 규정 위반이므로 추가 검사 없이 곧바로 위험으로 판정한다.

HazardBot 개발완료보고서

적색 · 가스 검출

적색 물질 — 가스 감지. 격납 파손

인화성 액체는 새어 나올 때 위험해진다. MQ-2가 가스를 검출하면 격납이 깨진 것으로 보고 위험으로 판정한다.

적색 · 가스 없음

적색 물질 — 가스 없음. 격납 유지, 통과

같은 적색이어도 가스가 없으면 격납이 유지된 상태다. 정상으로 판정하고 순찰을 이어간다.

10 / 20

즉시 위험

위험

통과

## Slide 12

03 · 개발 프로그램

적색 물질은 3초 정밀검사를 거친다

판정 노드가 검사를 요청하면 ENV 보드가 MQ-2를 3초간 샘플링하고, 5초 워치독이 응답 지연을 막는다

적색 판정
카메라가 적색 물체를 확인

검사 요청 발행
/hazard/gas_check_request

MQ-2 3초 샘플링
GAS_INSPECTION_DURATION_MS = 3000

결과 응답
/env/gas_result 로 회신

결과 유형

가스 검출 — 위험
격납이 깨진 것으로 보고 위험으로 판정한다. 초동 조치 대상이 된다.

DETECTED

가스 없음 — 통과
격납이 유지된 상태로 보고 정상 판정 후 순찰을 이어간다.

CLEAR

센서 오류 · 응답 없음
5초 워치독(GAS_CHECK_TIMEOUT_S = 5.0)이 걸리면 오류로 처리한다. 위험도 정상도 아닌 세 번째 결과다.

ERROR

샘플링 시간

3초

GAS_INSPECTION_DURATION_MS = 3000 — 액체가 새는지 확인하기에 필요한 최소 구간

HazardBot 개발완료보고서

응답 워치독

5초

GAS_CHECK_TIMEOUT_S = 5.0 — 응답이 늦어도 판정 흐름이 멈추지 않는다

결과 유형

3가지

DETECTED · CLEAR · ERROR — 오류도 판정 결과로 명시해 놓친 검사를 남기지 않는다

11 / 20

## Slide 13

03 · 개발 프로그램

사람의 시연 100회를 정책으로 학습했다

리더암으로 직접 보여준 동작을 ACT(Action Chunking Transformer)로 모방학습했다

시연 데이터를 쌓는 중 — 리더암은 사람 손에 있다
두 손으로 잡은 흰색 팔이 리더암, 섀시 위 팔이 팔로워암이다. 사람이 움직인 그대로 팔로워가 따라가고, 그때의 관절값이 학습 데이터가 된다. 노트북 화면에 뜬 것은 학습에 쓰는 손목 카메라 뷰다.

수집에서 롤아웃까지 3단계

01 · 시연 데이터 수집
리더-팔로워 구조라 사람이 보여준 궤적이 그대로 관절값으로 남는다. 적색 50 · 황색 50, 다섯 위치에 각 10회씩 배분해 100 에피소드를 모았다.

02 · ACT 정책 학습
한 스텝씩이 아니라 여러 스텝을 한 덩어리(청크)로 예측하는 ACT 로 학습한다. 중간에 멈추면 실패하는 파지 작업에 적합하다.

03 · 정책 롤아웃
학습된 정책이 카메라 관측을 받아 다음 청크를 내놓고 팔로워가 실행한다. 이 경로로 실물 30회를 측정했다.


시연 데이터

100 에피소드

색상 배분

적 50 · 황 50

학습량

100,000 스텝

학습 시간

4시간 47분

12 / 20

HazardBot 개발완료보고서

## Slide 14

03 · 개발 프로그램

집어서 넣고 뚜껑까지, 한 번에 수행한다

네 단계를 하나의 에피소드로 학습해 중간 개입 없이 이어서 실행한다

단일 에피소드 태스크

01 · 위험물 파지
정지 지점에 놓인 물체를 집는다. 파지가 실패하면 이후 단계가 모두 무의미해지는 가장 어려운 구간이다.

02 · 이동
집은 상태를 유지한 채 격리함 위치까지 팔을 옮긴다.

03 · 격리함 투입
격리함 안으로 물체를 넣고 그리퍼를 연다.

04 · 뚜껑 닫기
격리함 뚜껑을 덮어 취급구역에서 격리를 완료한다.

05 · 홈 복귀
3초 선형 보간으로 부드럽게 홈 포지션으로 돌아가 다음 지점에 대비한다.

HazardBot 개발완료보고서


01 위험물 파지 — 그리퍼가 적색 원통을 문다

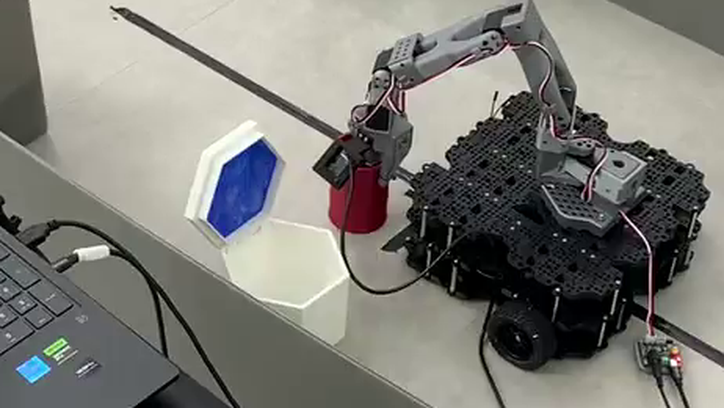
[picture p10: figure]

02 이동 — 집은 채로 들어 올려 옮긴다

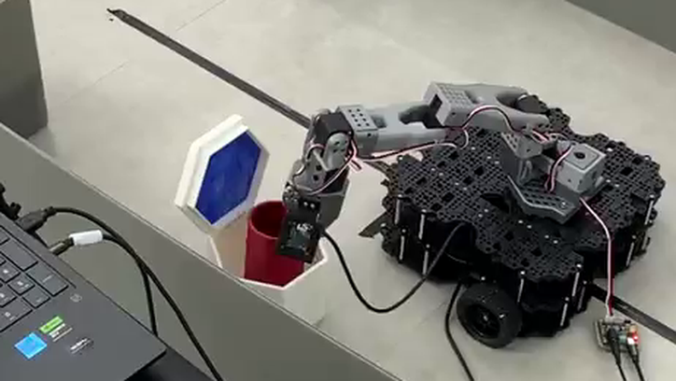
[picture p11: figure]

03 격리함 투입 — 격리함 안으로 내려놓는다


04 뚜껑 닫기 — 육각 뚜껑을 덮어 격리 완료

13 / 20

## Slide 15

03 · 개발 프로그램

판정에서 조치까지, 그리고 화면에 남는 기록

판정 노드가 위험을 알리면 오케스트레이터가 조치를 요청하고, 그 과정이 대시보드에 실시간으로 쌓인다

ROS2 통합 파이프라인

hazard_detector_node
색상과 가스 결과를 합쳐 최종 위험 판정

mission_orchestrator
조치 필요 여부 판단 · 전체 상태 관리

arm_act_node
lerobot-rollout 으로 ACT 정책 실행

결과 회신
성공 · 실패를 오케스트레이터로 되돌린다

HazardBot 개발완료보고서

RPi 가 호스팅하는 실시간 대시보드 — hazardbot.local:8080
EVENT LOG 한 화면에 세 판정이 다 남아 있다 — 황색 위반, 적색·가스 없음(통과), 적색·가스 감지(격납 파손). HAZARD LEVEL 은 종합 판정이 아니라 가스 지표라 황색 판정 때도 L0 다.

14 / 20


/hazard/detected

/arm/grip_request

/arm/act_result

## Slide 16

03 · 개발 프로그램

파지 30회, 판정 3케이스를 실물로 확인했다

ACT 파지는 성공률로, 규칙 기반 판정 로직은 케이스별 실물 시연으로 각각 검증했다

정지 위치별 ACT 파지 성공률

전체 30회 평균

rollout_plan.csv — 3세트 × 10회, 위치와 색상을 섞어 측정

판정 로직 실물 확인

규칙 기반 로직이라 확률적 정확도가 아니라, 케이스별로 실물에서 규칙대로 동작하는지를 확인했다.

근거리 (center · rear)
18회 중 18회 성공

100%

케이스

황색 — 산화성 고체

시연

3회

결과

즉시 위험 판정

원거리 (front)
12회 중 8회 성공

66.7%

적색 — 가스 검출

3회

위험 판정 · 격납 파손

86.7%

적색 — 가스 없음

1회

통과 · 격납 유지

ACT 파지 평균

86.7%

실물 30회 · 3세트 × 10회

근거리 위치

100%

center · rear 18회 전부 성공

원거리 위치

66.7%

front 12회 중 8회 성공 — 개선 여지

판정 로직 확인

7회

3케이스 전부 규칙대로 동작

15 / 20

HazardBot 개발완료보고서

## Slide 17

04 · 장애요인과 해결

막힌 지점마다 원인을 규명하고 우회했다

실물에서 만난 네 건을 증상 · 원인 · 해결로 정리했다 — 세 건은 원인까지 규명해 재발을 막았다

남은 한계
판정 → 초동 조치 자동 트리거는 코드 구현 후 실물 최종 검증이 남아 있다 · DRIVE 주행은 RPi/ESP 통합 이후 간헐적 오작동으로 이번 시연 범위에서 제외했다(안전 우선순위 판단 로직 자체는 구현되어 있다) · 원거리 위치 파지 성공률 66.7% 는 개선 여지가 있다.

증상

리더암 서보 6개 동시 소손
2026-06-16

원인

7.4V 정격 서보에 12V 오인가

해결

XL4015 두 대의 용도를 고정해(리더 7.4V / ESP32 5.0V) 레일을 물리적으로 분리하고, 되돌릴 수 없는 항목만 모은 통전 전 확인 5항목을 만들었다. 이후 동일 사고 0건.

ESP_Drive 보드 발열 사망
2026-08-25

핀소켓 GND가 모터 진동으로 이탈

전원선을 VCC/GND 직납땜으로 바꿨다. 이어서 전원 모듈(DFR0753)이 쇼트로 소손되자 XL4016 단독 레일로 계통을 우회 재구성했다.

표준 도구로 캘리브레이션 불가
2026-06~07

shoulder_lift 엔코더 래핑 · wrist_roll 연속 회전축 영점 불일치

표준 lerobot-calibrate 로는 잡히지 않아 축마다 전용 도구를 직접 만들었다. 정본 4종(leader_arm · follower_arm · wrist_zero · follower_home)을 확정하고 백업·복원 체계를 붙였다.

RPi 온보드 추론 중 정지
2026-08-04 사전점검 → 08-29 실물

수집 전 더미 가중치로 쟀을 때는 224×224 평균 0.509초로 합격이었다. 실물도 평균은 23ms 였지만, 청크를 다시 계산하는 틱만 1023ms 로 튀어 20초에 4번 멈췄다.

노트북 GPU 오프로드(gRPC)로 전환해 연결·제어까지 성공했으나 파지가 재현되지 않았다. 원인 미규명 상태로 조사를 종결하고, 노트북 단독 경로(rollout_act.ps1 · COM3 직결)로 제어 경로를 확정했다 — 15p 86.7%의 근거다.

HazardBot 개발완료보고서

16 / 20

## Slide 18

05 · 결과와 일정

발견에서 멈추지 않고 조치까지 간다

기존 순찰·보안 로봇과의 차이는 조치 여부, 판정 근거, 그리고 조작 방식 세 곳에서 갈린다

① 기존 산업용 순찰·보안 로봇과의 기능 비교

기존 로봇은 발견하고 알리는 데서 끝난다
결국 사람이 위험물에 다가가야 한다는 문제는 그대로 남는다. HazardBot 은 판정과 조치가 한 로봇 안에서 닫히므로, 사람이 현장에 들어가기 전에 격리라는 초동 조치가 이미 끝나 있다.

HazardBot 개발완료보고서

② 판정 근거

색이 아니라 물성으로 나눈다

고체 — 황색
가스를 내뿜지 않으므로 존재 자체가 위반이다. 즉시 판정한다.

액체 — 적색
새어 나올 때만 위험해지므로 MQ-2 3초 검사로 2차 게이팅한다.

기능

순찰 · 감시

기존 로봇

○

HazardBot

○

이상 감지 · 기록

○

○

관제 보고

○

○

물리적 초동 조치

×

○

③ 조치 방식

고정 궤적이 아니라 학습된 정책

모방학습 정책
좌표를 고정한 시퀀스가 아니라 사람 시연 100회를 학습한 ACT 정책이라, 물체 위치가 달라져도 대응한다.

설계 근거
판정 기준을 임의로 정하지 않고 위험물안전관리법 유별 혼재 제한과 KS C IEC 60079-10-1 에서 가져왔다.

17 / 20

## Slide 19

05 · 결과와 일정

임베디드 자원 제약을 구조로 풀었다

센서를 주기별로 나누고, 정지 권한을 한 곳에 모으고, 없는 자원은 다른 방법으로 대체했다

① 구조

역할이 분리된 3계층

센서를 「누가 이 데이터로 행동하는가」를 기준으로 세 계층으로 재편했다.

어떤 센서를 어느 보드에 붙일지가 논쟁이 아니라 규칙이 됐다. ToF 는 이 주기와 별개로 측정이 준비될 때만 읽고, 300mm 가 3회 연속이면 DRIVE 가 그 자리에서 모터를 끊는다.

HazardBot 개발완료보고서

② 안전

정지 권한을 한 곳에 모았다

모터를 멈추는 것은 DRIVE 뿐
하드웨어 풀다운 · DRIVE 로컬 · RPi · 사람의 4계층으로 나누되, 실제로 모터를 끊는 권한은 DRIVE 한 곳에만 둔다.

하트비트 — 명령이 아니라 생존 신호
STOP 을 보내는 방식이 아니라 생존 신호가 끊기면 멈추는 방식이라, RPi 사망 · WiFi 두절 · ENV 사망을 하나의 메커니즘으로 처리한다.

STBY 10kΩ 풀다운 페일세이프
ESP32 가 죽거나 리셋되면 제어핀이 하이임피던스가 되어 모터가 자동 정지한다. 설계 결정을 하드웨어로 뒷받침했다.

③ 자원

없는 자원은 다르게 대체했다

전압 피드포워드
엔코더 속도루프 없이 실제듀티 = 목표듀티 × (12.0 / 측정전압) 으로 배터리 전압 강하를 보상한다.

VL53L1X 논블로킹 읽기
블로킹으로 읽으면 라인 PID 주기가 붕괴함을 규명하고 구조를 바꿨다.

라인 추종 PD 루프
적분항 없이 KP=60 · KD=25 · 20ms(50Hz)로 구성했다. 센서 배선 없이 도는 가상 라인 모드로 조향 방향 · 비례 · 이탈 선회를 검증했고, 실측 게인 튜닝은 섀시 트랙 몫으로 남겼다.

18 / 20

계층

실시간 반사
라인센서 · 모터 제어

주기

20ms

담당

ESP_Drive

환경 감시
MQ-2 가스 · 화염

100ms

ESP_Env

인지 · 학습
카메라 · ACT

30fps

RPi · 노트북

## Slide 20

05 · 결과와 일정

사람이 위험물에 다가가는 횟수를 줄인다

지금 쓸 수 있는 곳과 기대효과, 그리고 실제 현장에 놓기 위해 넓혀야 할 네 축

활용성

어디에 놓을 수 있나

활용처

감시의 공백을 메운다
야간 · 연휴 · 교대 사이처럼 사람의 집중이 끊기는 시간대를 로봇이 같은 기준으로 이어서 지킨다.

사람이 도착하기 전에 격리가 끝나 있다
이상을 발견하고 사람이 현장에 투입되기까지의 시간 동안, 초동 조치인 격리가 이미 완료된 상태를 만든다.

판정 근거가 기록으로 남는다
색상값 · 가스값 · 시각이 EVENT LOG 에 쌓여 사후 확인과 원인 추적이 가능하다.

HazardBot 개발완료보고서

발전 가능성

현장에 놓기 위해 넓힐 네 축

위험물 분류 확장
지금은 색상 2분류뿐이다. 용기 라벨의 UN 번호와 QR/바코드를 읽어 MSDS(물질안전보건자료)와 연동하면 부식성 · 독성 · 압축가스까지 넓힐 수 있다.

초동 조치 범위 확장
격리함 투입 외에 밸브 잠금, 국소 배기 가동, 흡착제 · 중화제 살포, 스필 컨테인먼트 전개 같은 대응 동작으로 넓힌다.

온보드 자립 추론
지금은 ACT 정책이 노트북 GPU 에서 돌고 USB 로 팔을 제어한다. 현장에서는 로봇이 스스로 판단해야 하므로, 온보드 추론의 정지 원인을 규명하거나 엣지 NPU 가속기를 얹어 노트북 없이 도는 구조로 만든다.

전 구역 주행 · 다중 로봇
SLAM 기반 전 구역 주행으로 넓히고, 한 대로 감당할 수 없는 규모에는 구역 분담과 작업 핸드오프가 가능한 다중 로봇 구조로 확장한다.

19 / 20

반도체 FAB

정유 · 화학 플랜트

화학물질 보관창고

물류창고 야간 무인 시간대

소방 · 안전관리 초동 대응 보조

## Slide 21

05 · 결과와 일정

13주 공정과 세 명의 역할

2026-06-01부터 08-31까지 13주로 만들고, 9/1~9/3 사흘로 제출물을 냈다 — 순서는 기술적 선후관계로 정했다

개발 일정 — 2026-06-01 ~ 09-03 · 13주 + 제출 3일

계획 정본 · 저장소 · CI → 로봇팔 환경과 툴체인 → 전력 계통 설계·확정 → 3D 모델링 · 출력 → 캘리브레이션

캘리브레이션 정본 확정 → 텔레옵 마일스톤 → DRIVE 보드와 주행 펌웨어 → 안전 체계 · 센서 체계 설계

시나리오 · 시연 설계 정본 → 세트 제작과 실측 → 수집 게이트 · 준비 → ACT 수집 · 학습 · 검증

대회 양식 반영 → 필수항목 7개로 보고서 재구성 → 저장소 정본화 · 자격증명 정리 → 영상 자료 · 파일 구성

마일스톤

캘리브레이션 정본 4종 확정

★ 텔레옵 마일스톤 — 60초 오류 0건 · 평균 55.5Hz

시연 공간 확보 · 세트 제작 완료

★ ACT 학습 완료 — 100,000 스텝

저장소 정본화 — 추적 파일 259개 · ENV 펌웨어 반입

HazardBot 개발완료보고서

업무 분장

로봇팔 · 주행 · 전력 · 시연 설계
SO-101 리더-팔로워 구성, 시연 100회 수집과 ACT 정책 학습, RTX 4060 롤아웃 파이프라인 · ESP_Drive 펌웨어와 안전 우선순위 판단 로직 · 배터리부터 각 보드까지 전력 계통 전 구간 · 시나리오와 세트 설계

센서 하드웨어 · 펌웨어 · 시연 영상
MQ-2 가스센서와 화염센서 배선 · 납땜과 급전 경로 구성 · 센서 샘플링과 3초 가스 정밀검사(GAS_CHECK) 로직 구현 · 판정 결과(DETECTED / CLEAR / ERROR) 전달 통신 · 제출 시연 영상 제작

ROS2 통합 · 배포 · 저장소
ROS2 워크스페이스 구성과 노드 통합 · sensor_bridge_node 와 amr_bridge_node 를 통한 RPi–ESP 통신 연결 · RPi 실물 대시보드 배포와 실기 검증 · GitHub 저장소 관리

20 / 20

6월
W1–W5

7월
W6–W9

팀장

승환

8월
W10–W13

팀원

강희

9월
W14

07/11

팀원

07/16

08/14

진우

08/26

09/03

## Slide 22

감사합니다

HazardBot — 감지 · 판정에서 초동 조치까지

Q & A
남은 과제는 RPi 온보드 추론 경로의 원인 규명, 판정 → 조치 자동 연동의 실물 최종 검증, DRIVE 주행 재개다.

제24회 임베디드SW경진대회 · 자유공모 · 확정 후 삽입

2026-09-03

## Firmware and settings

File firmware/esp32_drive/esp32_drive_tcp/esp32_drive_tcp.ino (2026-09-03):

// HazardBot DRIVE — TCP 클라이언트 + VL53L1X ToF 통합 (2026-08-28)
//
// esp32_line_pid.ino(2026-08-21, 2채널 조향 + 정지점 마커)를 기반으로
// 8/25 에 확정된 통신 규격과 8/14 배선 정본의 ToF·배터리 분압을 얹은 것이다.
// 조향·마커 로직은 손대지 않았다 — 검증이 끝난 부분이라 그대로 옮겼다.
//
// ── 새로 들어온 것 ────────────────────────────────────────
//   1. TCP 클라이언트 — RPi 5 의 amr_bridge(포트 5000)에 붙는다.
//      🔴 서버는 RPi 다. ESP32 가 접속하러 간다 (amr_bridge_node.py:tcp_server).
//   2. <SENS> 주기 송신 + <MOVE>/<STOP>/<HB> 수신, 체크섬 검증
//   3. VL53L1X ToF — 🔴 논블로킹 읽기. 300mm 장애물 정지(안전 계층 1)
//   4. 배터리 분압 40k/10k = x5.0 → G39. 전압 피드포워드 + 과방전 감시
//   5. RPI_TIMEOUT 페일세이프 — 하트비트가 끊기면 스스로 선다
//   6. 🟠 <DETECT>/<RETURN>/<RETDONE> (2026-08-28 추가, 진우 제안 프로토콜)
//      정지 마커 도달마다 <DETECT> 1회 송신(비전 캡처 트리거) · <RETURN> 수신 시
//      개루프 후진 · 후진 끝나면 <RETDONE> 1회 송신. 🔴 RPi 쪽(mission_orchestrator·
//      amr_bridge)엔 이 프로토콜을 실제로 쓰는 코드가 아직 없다 — DRIVE 쪽만 먼저
//      준비해둔 것이다. RETURN_DURATION_MS·RETURN_SPEED 는 실측 전 잠정값이다(§10 참고)
//
// ── 🔴 통전 전에 반드시 ───────────────────────────────────
//   🔴 VCC 와 GND 는 직납땜이다. 핀소켓에 물리지 않는다.
//   지난 보드는 GND 를 핀소켓으로 물려뒀는데 그 접점이 **모터 진동으로 빠져** 죽었다.
//   3V3 에 매달린 주변부 전류(60~90mA) 전량이 신호선을 타고 GPIO 보호 다이오드로
//   귀환하면서 발열 → 사망. USB 는 자기 GND 를 들고 오므로 이 상태에서도
//   업로드는 계속 성공한다. 그래서 안 보인다.
//
//   🔴 도통 확인은 하되, 그것만으로는 부족하다 — 진동형 고장은 정지 상태에서
//   통해 있어도 주행 중에 빠진다. **모터를 돌린 뒤 한 번 더** 짚는다.
//   GND 핀 2개 이상(DevKit V1 은 3개) · TB6612 GND 3패드 전부 · 라인센서 GND.
//
//   🔴 직납땜의 대가로 OTA 가 필수가 된다 — 보드를 기판에서 뽑을 수 없으니
//   「주변 회로 분리 후 USB 업로드」가 안 된다. 그래서 이 스케치의 ArduinoOTA
//   (`hazardbot-drive`)는 편의가 아니라 전제다. 12V 인가 중 USB 업로드 금지.
//   🔴 뜨거우면 즉시 분리 — 발열은 진단 신호가 아니라 파괴가 진행 중이라는 뜻이다.

#include <WiFi.h>
#include <ArduinoOTA.h>
#include <ESPmDNS.h>

// ══════════════════════════════════════════════════════════
// 0. 🔲 현장에서 채워야 하는 값 — 업로드 전에 확인할 것
// ══════════════════════════════════════════════════════════
// 🔵 2026-08-29 — 아이폰 핫스팟(Hwan) 대신 RPi 자체 AP로 전환.
//    "핫스팟이 유휴 시 광고를 멈춰 ESP32가 재접속 못 함" 문제(firmware/README.md
//    트러블슈팅표)가 RPi AP로 가면서 없어진다 — RPi는 상시 켜져 있으니까.
const char* WIFI_SSID = "여기에-AP-SSID";
const char* WIFI_PW   = "여기에-AP-비밀번호";  // 🔴 공개 저장소라 실제 값을 적지 않는다. 업로드 전에 여기만 채울 것.

// 🔴 RPi 5 의 주소. 고정 IP 를 쓰면 여기에 적고, DHCP 면 빈 문자열로 두고
//    아래 RPI_MDNS 로 찾게 한다 (RPi 에서 `hostname -I` 로 확인).
// 🔵 2026-08-29 — RPi AP 모드의 고정 IP를 안 받아서 일단 mDNS로 간다.
//    비어있으면 tryConnect() 가 MDNS.queryHost(RPI_MDNS) 로 찾는다.
//    🟠 AP 환경에서 mDNS/멀티캐스트가 막혀 있으면 이 방식이 실패할 수 있다 —
//    "RPi 주소를 못 찾았다" 로그가 반복되면 RPi 의 AP 모드 IP(보통 192.168.4.1)를
//    알아내서 여기 직접 적는 걸로 바꿀 것.
const char* RPI_HOST  = "";
const char* RPI_MDNS  = "hazardbot";      // RPI_HOST 가 비었을 때만 사용 (hazardbot.local)
const uint16_t RPI_PORT = 5000;           // amr_bridge_node.py: AMR_PORT = 5000

// ToF(VL53L1X) — 장애물 정지 계층. 컴파일하려면 라이브러리가 하나 더 필요하다:
//    Arduino IDE > 라이브러리 매니저 > "Adafruit VL53L1X" (의존성 Adafruit BusIO 는 같이 깔린다)
//
// 🔵 2026-08-30 — 라인추종 단독 벤치 테스트 중 ToF 가 계속 정지를 걸어서 0 으로 껐다.
// 🔵 2026-09-03 — 다시 1 로 되돌린다. 장애물 정지는 안전 구조의 일부라 빼놓을 수 없다.
//
//    0 이면 장애물 정지 계층이 통째로 사라진다. obstacleNear 를 세팅하는 곳이
//    pollToF() 뿐인데 그 함수 본문이 HAS_TOF=0 이면 비기 때문이다. 이때
//    motionBlocked() 는 tofOk 를 안 보므로 주행은 그대로 되고 fault 만 SENSOR 로
//    뜬다 — 즉 "정지가 없어진 줄 모르고 도는" 상태가 된다.
//
//    🔴 벤치에서 오정지가 재현되더라도 여기를 0 으로 되돌리지 말 것.
//    먼저 OBSTACLE_STOP_MM(현재 300) 을 낮추거나 OBSTACLE_STREAK(현재 3) 을 올린다.
//    센서가 없거나 begin() 이 실패하면 tofOk=false 로 남아 주행을 막지 않고
//    dist 가 -1, fault 가 SENSOR 로 나간다 — 안전한 쪽으로 실패한다.
#define HAS_TOF 1

#if HAS_TOF
  #include <Wire.h>
  #include <Adafruit_VL53L1X.h>
  Adafruit_VL53L1X tof;
#endif

// ══════════════════════════════════════════════════════════
// 1. 핀 — firmware/README.md §1 · 전력계통_실배선_2026-08-28.md 2부 §1.5
// ══════════════════════════════════════════════════════════
#define PIN_PWMA   25
#define PIN_AIN1   26
#define PIN_AIN2   27
#define PIN_PWMB   14
#define PIN_BIN1   16      // 보드에 RX2 로 인쇄된 경우가 많다
#define PIN_BIN2   17      // 〃 TX2
#define PIN_STBY    4
#define PIN_LINE_L 13      // 2채널 교체분 (기존 S1 자리)
#define PIN_LINE_R 32      // 〃        (기존 S5 자리)
#define PIN_TOF_SDA 21
#define PIN_TOF_SCL 22
#define PIN_BATT   39      // 실크스크린 SN / VN — EN 버튼 옆. 입력 전용

const bool LINE_ACTIVE_LOW = false;   // 검정에서 HIGH — 실측으로 재확인할 것

// ══════════════════════════════════════════════════════════
// 2. 확정값
// ══════════════════════════════════════════════════════════
const int PWM_FREQ = 20000, PWM_BITS = 8, PWM_MAX = 255;

// ── 조향 (esp32_line_pid.ino 에서 그대로) ──
// 🔵 2026-08-30 — 감속 마커 폐기(정지 마커만 사용)로 마커 도달 시 감속 없이 바로
//    풀스피드→급정지가 된다. 마커 오버런을 줄이려고 baseSpeed를 낮췄다(120→95).
int turnDelta     = 40;
int baseSpeed     = 95;
int approachSpeed = 70;   // 🔴 감속 마커 폐기로 지금은 미사용(phase가 PH_APPROACH로 안 감) — 죽은 값은 아니고 부활 대비로 남겨둠
const int CONTROL_MS = 20;

// ── RETURN(후진) — 🟠 전부 잠정값, 실측 전 ──
// 오도메트리가 없어 개루프(시간×속도)로만 갈 수 있다. 목표는 "후진 800mm"(8/25 이월
// 목록)였는데 이 상수들로 실제로 몇 mm 가는지는 벤치에서 자로 재기 전엔 아무도 모른다.
// 촬영 전 반드시: 시리얼 'r' 키로 후진시켜보고 거리 재서 RETURN_DURATION_MS 조정할 것.
int RETURN_SPEED           = 80;    // 🔵 baseSpeed와 같이 낮췄다(100→80). baseSpeed보다 낮게 — 후진은 조향 보정이 없다
unsigned long RETURN_DURATION_MS = 1500;

// ── 통신 — 8/25 §0-B.G 확정 ──
const unsigned long SENS_PERIOD_MS = 300;    // <SENS> 송신 주기 (하트비트 주기와 동일)
// 🔵 2026-08-30 — 1000ms→3000ms. 실측해보니 모터 기동 직후 0.6~1초 사이에 WiFi가
// 순간 끊겨 RPI_TIMEOUT이 걸리는 패턴이 재현됨(ENV 보드는 그 구간에도 안 끊김 —
// RPi/AP 문제가 아니라 DRIVE 자신의 모터 기동 전류로 인한 순간 전압강하로 추정).
// 근본 원인(전원 디커플링)은 별도 점검 필요 — 이건 그 사이 임시 완화값이다.
const unsigned long RPI_TIMEOUT_MS = 3000;
                                             // 🔴 RPi 가 실제로 0.5s 주기로 쏘면 여유가 없다.
                                             //    복구일에 실측해서 확정한다 (8/25 §1 ③)
const unsigned long RECONNECT_MS   = 2000;   // TCP 재접속 간격

// ── ToF — 배선_확정 §3 · 구역_마커_설계 §6.1 ──
const uint16_t OBSTACLE_STOP_MM = 300;   // 🔵 300mm 단일 상수 (8/18 개정, 구간별 전환 폐기)
const uint16_t OBSTACLE_CLEAR_MM = 380;  // 히스테리시스 — 경계에서 덜덜거리지 않게
const uint8_t  OBSTACLE_STREAK   = 3;    // 연속 3회여야 인정 (단발 오검출 차단)

// ── 배터리 — 배선_확정 §2 ② ──
const float BATT_DIVIDER   = 5.0f;    // 40k/10k. 계수가 정확히 5.0 이라 코드가 깔끔하다
float       battCalib      = 1.0f;    // 🔲 멀티미터 실측 보정. 0.8~1.5 로 클램프
const float BATT_CUTOFF_V  = 9.9f;    // 3S 과방전 하한
const float BATT_WARN_V    = 10.5f;
const float BATT_NOMINAL_V = 12.0f;   // 전압 피드포워드 기준

// ── 마커 (esp32_line_pid.ino 에서 그대로) ──
const unsigned long MARKER_GUARD_MS = 1000;
const int SHORT_BRAKE_MS = 150;

// ══════════════════════════════════════════════════════════
// 3. 프로토콜 코드 — amr_bridge_node.py 의 이름 배열과 순서가 같아야 한다
// ══════════════════════════════════════════════════════════
enum StateCode  { ST_SAFE = 0, ST_WARNING, ST_DANGER, ST_STOP, ST_SENSOR_ERROR };
enum ActionCode { AC_NORMAL = 0, AC_LIMITED, AC_STOP };
enum FaultCode  { FT_OK = 0, FT_ESTOP, FT_LIPO, FT_SENSOR, FT_RPI_TIMEOUT, FT_HAZARD };

// ══════════════════════════════════════════════════════════
// 4. 상태
// ══════════════════════════════════════════════════════════
enum Phase { PH_CRUISE, PH_APPROACH };
enum DriveMode { DM_LINE, DM_REMOTE };   // 라인추종 자율 / RPi 의 <MOVE> 원격

Phase     phase      = PH_CRUISE;
DriveMode driveMode  = DM_LINE;

int   stopIndex   = 0;          // 🔵 0~3 순환 (8/25 §0-B.G ④). 이전 스케치는 1~4 였다
int   blackStreak = 0;
bool  markerLatch = false;
unsigned long lastMarkerMs = 0;

// 🔵 2026-08-30 — 소프트스타트. 정지 상태에서 목표 듀티로 바로 점프하면 모터 기동
// 인러시로 순간 전압강하가 생겨 WiFi가 끊기는 패턴이 실측으로 재현됨. 출발(pidRunning
// 이 true 되는 시점)마다 0→목표 듀티를 DRIVE_RAMP_MS에 걸쳐 올린다. RETURN/MOVE 는
// 아직 대상이 아니다 — 우선 재현됐던 라인추종 출발 구간만 다룬다.
const unsigned long DRIVE_RAMP_MS = 400;
unsigned long driveRampStartMs = 0;

bool  motorsEnabled = false;
bool  pidRunning    = false;
bool  useRealSensor = true;
bool  simL = false, simR = false;

// RETURN(후진) 진행 상태 — 🔵 controlStep() 맨 위에서 다른 구동 모드보다 먼저 본다
bool  returning      = false;
unsigned long returnStartMs = 0;

int   dutyL = 0, dutyR = 0;
int   remoteL = 0, remoteR = 0;   // <MOVE> 로 받은 목표 듀티

// 페일세이프 플래그
bool  estopLatched   = false;
bool  rpiTimeout     = false;
bool  obstacleNear   = false;
bool  battCritical   = false;
bool  tofOk          = false;
bool  everConnected  = false;   // 한 번이라도 amr_bridge 에 붙은 적이 있는가
uint8_t obstacleStreak = 0;

int32_t distanceMm = -1;    // -1 = 미측정
float   battVolts  = 0.0f;

WiFiClient rpi;
unsigned long lastHbMs = 0, lastSensMs = 0, lastCtrlMs = 0;
unsigned long lastTryConnMs = 0, lastTelemMs = 0;
char rxBuf[128];
uint8_t rxLen = 0;

// ══════════════════════════════════════════════════════════
// 5. 모터
// ══════════════════════════════════════════════════════════
void setMotor(int in1, int in2, int pwmPin, int duty) {
  if (duty >= 0) { digitalWrite(in1, HIGH); digitalWrite(in2, LOW); }
  else           { digitalWrite(in1, LOW);  digitalWrite(in2, HIGH); duty = -duty; }
  ledcWrite(pwmPin, min(duty, PWM_MAX));
}

void applyDrive(int l, int r) {
  dutyL = l; dutyR = r;
  setMotor(PIN_AIN1, PIN_AIN2, PIN_PWMA, l);
  setMotor(PIN_BIN1, PIN_BIN2, PIN_PWMB, r);
}

void stopMotors() {
  applyDrive(0, 0);
  pidRunning = false;
  phase = PH_CRUISE;
  blackStreak = 0; markerLatch = false;
  remoteL = remoteR = 0;
}

void doStop() {   // 숏브레이크 — 양쪽 HIGH 로 단락 제동
  digitalWrite(PIN_AIN1, HIGH); digitalWrite(PIN_AIN2, HIGH);
  digitalWrite(PIN_BIN1, HIGH); digitalWrite(PIN_BIN2, HIGH);
  ledcWrite(PIN_PWMA, PWM_MAX);
  ledcWrite(PIN_PWMB, PWM_MAX);
  delay(SHORT_BRAKE_MS);
  applyDrive(0, 0);
}

void setEnabled(bool on) {
  motorsEnabled = on;
  digitalWrite(PIN_STBY, on ? HIGH : LOW);
  if (!on) stopMotors();
}

// 🔴 하나라도 서면 바퀴가 돌면 안 되는 조건들
bool motionBlocked() {
  return estopLatched || rpiTimeout || obstacleNear || battCritical || !motorsEnabled;
}

// ══════════════════════════════════════════════════════════
// 6. 라인센서 · 마커 (esp32_line_pid.ino 에서 그대로)
// ══════════════════════════════════════════════════════════
bool readL() {
  if (!useRealSensor) return simL;
  int v = digitalRead(PIN_LINE_L);
  return LINE_ACTIVE_LOW ? (v == LOW) : (v == HIGH);
}
bool readR() {
  if (!useRealSensor) return simR;
  int v = digitalRead(PIN_LINE_R);
  return LINE_ACTIVE_LOW ? (v == LOW) : (v == HIGH);
}

void onMarker() {
  // 🔵 2026-08-30 — 감속 마커 폐기. 마커 하나(정지 마커)만 쓴다 — 두 마커를 기다리던
  // 2단계 로직(1번째: PH_APPROACH 진입 / 2번째: 정지)을 걷어내고 첫 마커에서 바로 선다.
  doStop();
  stopIndex = (stopIndex + 1) % 4;      // 🔵 0~3 순환
  pidRunning = false;
  phase = PH_CRUISE;
  blackStreak = 0; markerLatch = false;
  Serial.printf(">>> 정지 마커 — stopIndex=%d 도달. 정지 완료.\n", stopIndex);

  // 🟠 8/28 추가 — 정지점마다 무조건 1회 보낸다. 구역별로 가려 보내지 않는다
  // (stopIndex↔ZONE 매핑이 RPi 쪽에도 아직 없다). 물체 없는 정지점이면 vision_node 가
  // "감지된 물체 없음"으로 넘어갈 뿐이라 무해하다.
  sendFrame("DETECT");
  Serial.println(F(">>> DETECT 송신"));
}

void checkMarker() {
  if (!useRealSensor) return;
  bool allBlack = readL() && readR();
  if (allBlack) blackStreak++;
  else { blackStreak = 0; markerLatch = false; }

  if (blackStreak >= 2 && !markerLatch && (millis() - lastMarkerMs) > MARKER_GUARD_MS) {
    markerLatch = true;
    lastMarkerMs = millis();
    onMarker();
  }
}

// ══════════════════════════════════════════════════════════
// 7. 배터리 — 전압 피드포워드 + 과방전 감시
// ══════════════════════════════════════════════════════════
void readBattery() {
  // analogReadMilliVolts 는 eFuse 캘리브레이션을 쓴다 — 생 analogRead 보다 정확하다
  uint32_t mv = analogReadMilliVolts(PIN_BATT);
  battVolts = (mv / 1000.0f) * BATT_DIVIDER * battCalib;
  battCritical = (battVolts > 1.0f) && (battVolts < BATT_CUTOFF_V);
  // 1.0V 미만이면 분압이 아직 안 붙은 것으로 보고 판정하지 않는다 (벤치에서 오탐 방지)
}

// 배터리가 빠지면 같은 듀티로도 느려진다 — 12.0V 기준으로 되돌린다
int feedForward(int duty) {
  if (battVolts < 6.0f) return duty;      // 분압 미배선 상태면 보정하지 않는다
  float k = BATT_NOMINAL_V / battVolts;
  if (k < 0.8f) k = 0.8f;
  if (k > 1.5f) k = 1.5f;
  return constrain((int)(duty * k), -PWM_MAX, PWM_MAX);
}

// ══════════════════════════════════════════════════════════
// 8. ToF — 🔴 논블로킹. dataReady() 가 false 면 그냥 지나간다
// ══════════════════════════════════════════════════════════
void setupToF() {
#if HAS_TOF
  Wire.begin(PIN_TOF_SDA, PIN_TOF_SCL, 100000);   // 100kHz (배선_확정 §3)
  if (!tof.begin(0x29, &Wire)) {
    Serial.println(F("🔴 VL53L1X 초기화 실패 — 배선(G21/G22)·3V3 확인. ToF 없이 계속한다"));
    tofOk = false;
    return;
  }
  tof.startRanging();
  tof.setTimingBudget(50);
  tofOk = true;
  Serial.println(F("VL53L1X OK (논블로킹 모드)"));
#else
  Serial.println(F("ToF 비활성 (HAS_TOF=0)"));
  tofOk = false;
#endif
}

void pollToF() {
#if HAS_TOF
  if (!tofOk) return;
  if (!tof.dataReady()) return;        // 🔴 절대 기다리지 않는다
  int16_t d = tof.distance();
  tof.clearInterrupt();
  if (d < 0) return;                   // 측정 실패 프레임은 버린다
  distanceMm = d;

  if (!obstacleNear) {
    if (distanceMm <= OBSTACLE_STOP_MM) {
      if (++obstacleStreak >= OBSTACLE_STREAK) {
        obstacleNear = true;
        Serial.printf("🔴 장애물 %ldmm — 계층1 정지\n", (long)distanceMm);
        doStop();
        pidRunning = false;
      }
    } else obstacleStreak = 0;
  } else {
    if (distanceMm >= OBSTACLE_CLEAR_MM) {   // 히스테리시스로 해제
      obstacleNear = false;
      obstacleStreak = 0;
      Serial.printf("🔵 장애물 해제 %ldmm\n", (long)distanceMm);
    }
  }
#endif
}

// ══════════════════════════════════════════════════════════
// 9. 프로토콜 — amr_bridge_node.py 와 바이트 단위로 같아야 한다
//
//   프레이밍 : <payload,CS>\n
//   체크섬   : payload(쉼표 포함, CS 제외) 각 문자의 ASCII 합 % 256
//              → Python: sum(ord(c) for c in ','.join(parts[:-1])) % 256
//
//   올림 : <SENS,gas,flame,battCv,state,action,fault,dist,stopIdx,CS>
//   내림 : <MOVE,left,right,CS> · <STOP,CS> · <HB,CS>
//
//   🟠 2026-08-28 추가(진우 제안, RPi 쪽 구현 아직 없음) —
//   올림 : <DETECT,CS>   정지 마커 도달마다 1회 — RPi 는 이걸 비전 캡처 트리거로 쓴다
//   올림 : <RETDONE,CS>  RETURN 후진이 끝났을 때 1회
//   내림 : <RETURN,CS>   수신하면 즉시 개루프 후진 시작(§10 controlStep 참고)
// ══════════════════════════════════════════════════════════
uint8_t calcChecksum(const char* payload) {
  uint32_t s = 0;
  for (const char* p = payload; *p; ++p) s += (uint8_t)(*p);
  return (uint8_t)(s % 256);
}

void sendFrame(const char* payload) {
  if (!rpi.connected()) return;
  char out[160];
  snprintf(out, sizeof(out), "<%s,%u>\n", payload, (unsigned)calcChecksum(payload));
  rpi.print(out);
}

uint8_t currentState() {
  if (estopLatched || rpiTimeout)   return ST_STOP;
  if (obstacleNear || battCritical) return ST_DANGER;
  if (!tofOk)                       return ST_SENSOR_ERROR;
  if (phase == PH_APPROACH || battVolts < BATT_WARN_V) return ST_WARNING;
  return ST_SAFE;
}

uint8_t currentAction() {
  if (motionBlocked())         return AC_STOP;
  if (phase == PH_APPROACH)    return AC_LIMITED;
  return AC_NORMAL;
}

uint8_t currentFault() {
  if (estopLatched)  return FT_ESTOP;
  if (rpiTimeout)    return FT_RPI_TIMEOUT;
  if (battCritical)  return FT_LIPO;
  if (obstacleNear)  return FT_HAZARD;
  if (!tofOk)        return FT_SENSOR;
  return FT_OK;
}

void sendSens() {
  // 🔴 gas·flame 은 항상 0 이다 — 이 보드에는 가스·화염 센서가 없다.
  //    7/20 재분할로 MQ-135 · KY-026 은 전부 ENV(강희) 로 갔다.
  //    자리를 비우지 않고 0 으로 채우는 이유: amr_bridge 가 필드 위치로 파싱하므로
  //    빼는 순간 뒤 필드가 전부 한 칸씩 밀린다. 진우의 파서 정리와 같은 커밋으로만 뺀다.
  //
  //    🔴 그래서 지금 /amr/gas 는 항상 0 이다. hazard_detector 구독을 /env/* 로
  //    옮기기 전까지 가스 판정이 조용히 죽어 있다는 뜻이다 (8/25 §5.1-C).
  //
  // 🔵 dist·stopIdx 는 faultCode 뒤에 "덧붙였다" — 기존 파서와 호환된다.
  //    amr_bridge 는 len(parts) >= 8 과 parts[1..6] 만 보고, 체크섬은 parts[:-1]
  //    전체로 계산하므로 필드가 늘어도 깨지지 않는다.
  int battCv = (int)(battVolts * 100.0f + 0.5f);
  char payload[128];
  snprintf(payload, sizeof(payload), "SENS,0,0,%d,%u,%u,%u,%ld,%d",
           battCv, (unsigned)currentState(), (unsigned)currentAction(), (unsigned)currentFault(),
           (long)distanceMm, stopIndex);
  sendFrame(payload);
}

// 수신 한 줄 처리
void handleLine(char* line) {
  int n = strlen(line);
  if (n < 3 || line[0] != '<' || line[n - 1] != '>') return;

  line[n - 1] = '\0';           // '>' 제거
  char* inner = line + 1;       // '<' 건너뜀

  char* lastComma = strrchr(inner, ',');
  if (!lastComma) return;

  int rxCs = atoi(lastComma + 1);
  *lastComma = '\0';            // inner 는 이제 CS 를 뺀 payload
  if (calcChecksum(inner) != (uint8_t)rxCs) {
    Serial.printf("체크섬 불일치: %s (기대 %u, 수신 %d)\n",
                  inner, (unsigned)calcChecksum(inner), rxCs);
    return;
  }

  lastHbMs = millis();          // 🔴 유효 프레임은 전부 하트비트로 친다
  if (rpiTimeout) {
    rpiTimeout = false;
    Serial.println(F("🔵 RPi 하트비트 복구"));
  }

  char* cmd = strtok(inner, ",");
  if (!cmd) return;

  if (strcmp(cmd, "HB") == 0) {
    return;                                     // 위에서 이미 갱신했다

  } else if (strcmp(cmd, "STOP") == 0) {
    estopLatched = true;
    doStop();
    pidRunning = false;
    Serial.println(F("🔴 <STOP> 수신 — 비상 정지 래치"));

  } else if (strcmp(cmd, "MOVE") == 0) {
    char* sL = strtok(NULL, ",");
    char* sR = strtok(NULL, ",");
    if (!sL || !sR) return;
    remoteL = constrain(atoi(sL), -PWM_MAX, PWM_MAX);
    remoteR = constrain(atoi(sR), -PWM_MAX, PWM_MAX);
    driveMode = DM_REMOTE;
    pidRunning = false;                         // 원격 중엔 라인추종을 끈다

  } else if (strcmp(cmd, "GO") == 0) {
    // 🔵 2026-08-30 — RPi 원격 시작 지원. 시리얼 'g' 와 동일하게 동작한다
    // (amr_bridge_node.py 의 send_go() 가 이제 실제로 보낸다).
    setEnabled(true);
    estopLatched = false;
    driveMode = DM_LINE;
    pidRunning = true; phase = PH_CRUISE;
    blackStreak = 0; markerLatch = false;
    driveRampStartMs = millis();
    Serial.println(F("🔵 <GO> 수신 — 라인추종 시작 (CRUISE) · ESTOP 해제"));

  } else if (strcmp(cmd, "RETURN") == 0) {
    // 🟠 8/28 추가. ESTOP 은 건드리지 않는다 — 이미 래치돼 있으면 motionBlocked() 가
    //    controlStep() 에서 그대로 막는다. 이미 후진 중이면 타이머를 다시 시작하지 않는다.
    if (!returning) {
      returning = true;
      returnStartMs = millis();
      pidRunning = false;
      driveMode = DM_LINE;
      Serial.println(F("🔴 <RETURN> 수신 — 후진 시작"));
    }
  }
}

void pollRpi() {
  while (rpi.available()) {
    char c = rpi.read();
    if (c == '\n' || c == '\r') {
      if (rxLen > 0) { rxBuf[rxLen] = '\0'; handleLine(rxBuf); rxLen = 0; }
    } else if (rxLen < sizeof(rxBuf) - 1) {
      rxBuf[rxLen++] = c;
    } else {
      rxLen = 0;              // 넘치면 버린다
    }
  }
}

void tryConnect() {
  if (rpi.connected()) return;
  if (millis() - lastTryConnMs < RECONNECT_MS) return;
  if (WiFi.status() != WL_CONNECTED) return;

  // 🔴 바퀴가 도는 동안에는 접속을 시도하지 않는다.
  //    connect() 도 mDNS queryHost() 도 수백 ms 를 막는데, 20ms 조향 루프가
  //    그만큼 서면 라인에서 이탈한다. 연결이 끊기면 어차피 RPI_TIMEOUT 이
  //    먼저 로봇을 세우므로, 선 다음에 붙으면 된다.
  if (dutyL != 0 || dutyR != 0) return;

  lastTryConnMs = millis();

  IPAddress ip;
  bool have = false;
  if (RPI_HOST && RPI_HOST[0] && ip.fromString(RPI_HOST)) {
    have = true;
  } else {
    ip = MDNS.queryHost(RPI_MDNS);              // hazardbot.local · 🟠 최대 1초 블로킹
    have = (ip != IPAddress((uint32_t)0));
  }
  if (!have) { Serial.println(F("RPi 주소를 못 찾았다 — RPI_HOST 확인")); return; }

  Serial.printf("amr_bridge 접속 시도 %s:%u ... ", ip.toString().c_str(), RPI_PORT);
  if (rpi.connect(ip, RPI_PORT, 500)) {         // 🔵 타임아웃 500ms — 기본값은 훨씬 길다
    rpi.setNoDelay(true);
    rxLen = 0;
    lastHbMs = millis();                        // 접속 직후 타임아웃 오탐 방지
    rpiTimeout = false;
    everConnected = true;
    Serial.println(F("연결됨"));
  } else {
    Serial.println(F("실패"));
  }
}

void checkRpiTimeout() {
  bool stale = (millis() - lastHbMs) > RPI_TIMEOUT_MS;
  if (rpi.connected() && stale && !rpiTimeout) {
    rpiTimeout = true;
    doStop();
    pidRunning = false;
    Serial.println(F("🔴 RPI_TIMEOUT — 하트비트 끊김. 정지"));
  }
  // 🔴 한 번 붙었다가 끊긴 것은 즉시 정지 사유다.
  //    반대로 "한 번도 안 붙은" 상태는 벤치 단독 주행이므로 막지 않는다 —
  //    RPi 없이 조향·마커를 튜닝하는 것이 이 스케치의 다른 절반이다.
  if (!rpi.connected() && everConnected && !rpiTimeout) {
    rpiTimeout = true;
    doStop();
    pidRunning = false;
    Serial.println(F("🔴 TCP 끊김 — 정지 (한 번 붙었던 연결이다)"));
  }
}

// ══════════════════════════════════════════════════════════
// 10. 제어 루프
// ══════════════════════════════════════════════════════════

// RETURN 종료 — 정상 완료(completed=true)면 RETDONE 을 보낸다.
// motionBlocked() 로 인한 중단(completed=false)이면 안 보낸다 — STOP/EMERGENCY 가
// 이미 그 경로를 따로 처리하고 있고, "후진을 완료 못 했다"고 RPi 가 알 필요는 없다
// (RPi 는 하트비트/STOP 으로 이미 알고 있다).
void endReturn(bool completed) {
  returning = false;
  applyDrive(0, 0);
  pidRunning = false;
  phase = PH_CRUISE;
  if (completed) {
    Serial.println(F(">>> RETURN 완료 — RETDONE 송신"));
    sendFrame("RETDONE");
  } else {
    Serial.println(F("🔴 RETURN 중단(정지 사유 발생) — RETDONE 미송신"));
  }
}
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
void loop() {
  ArduinoOTA.handle();
  handleSerial();

  tryConnect();
  pollRpi();
  checkRpiTimeout();
  pollToF();

  if (millis() - lastCtrlMs >= CONTROL_MS) {
    lastCtrlMs = millis();
    readBattery();
    controlStep();
    if (driveMode == DM_LINE && pidRunning) checkMarker();
  }

  if (millis() - lastSensMs >= SENS_PERIOD_MS) {
    lastSensMs = millis();
    sendSens();
  }

  if (millis() - lastTelemMs >= 1000) {
    lastTelemMs = millis();
    printStatus();
  }
}

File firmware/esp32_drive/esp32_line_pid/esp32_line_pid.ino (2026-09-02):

// HazardBot 라인트레이싱 조향 + 정지점 마커 검출 — 2채널 버전 (2026-08-21)
//
// ── 왜 2채널인가 ──────────────────────────────────────────
//   기존 5채널 IR 라인센서 보드가 흑/백을 구분 못하는 고장으로 판단되어,
//   독립된 1채널 IR 반사센서 2개(좌/우)로 교체했다.
//
// ── 장착 방식 — 중요 ──────────────────────────────────────
//   두 센서를 **라인 폭보다 넓게** 벌려 장착한다. 평소(직진 중)에는
//   라인이 두 센서 "사이"에 있어 **둘 다 흰 바닥(0)** 을 본다.
//   이래야 "둘 다 검정(1,1)" 이 마커(전폭 가로선)에서만 뜨는 고유 신호가 된다.
//   센서를 라인 가장자리/위에 걸치게 달면 평상시에도 (1,1) 이 나와
//   마커와 구분이 안 된다.
//
// ── 5채널 대비 알려진 한계 (감수하기로 한 트레이드오프) ──────
//   1. 연속 위치값이 없다 — 왼쪽만 감지/오른쪽만 감지/둘 다/둘 다 아님, 4상태뿐.
//      부드러운 비례 제어가 아니라 **온-오프에 가까운 제어**라 더 덜컹거릴 수 있다.
//   2. **완전히 라인을 잃었을 때를 구분할 수 없다.** 두 센서가 모두 흰 바닥을
//      보는 상태는 "정상 중앙" 과 "너무 멀리 벗어나 아예 안 보임" 이 **같은 신호(0,0)** 다.
//      → 크게 벗어나면 그대로 직진하며 못 돌아올 수 있다. 별도 복구 로직이 없다.
//   3. 마커 오검출 여유가 줄었다 — 5개 중 5개 조건이 2개 중 2개가 되어
//      급커브에서 라인이 순간적으로 양쪽에 다 걸리면 마커로 오인될 수 있다.
//
// 두 가지 입력 모드:
//   가상 모드(기본) — 시리얼로 좌/우 감지 상태를 흉내 낸다. 바퀴 띄우고 방향 검증용.
//   실측 모드('v')  — 실제 센서 2개를 읽는다.
//
// ── 정지점 마커 (firmware/구역_마커_설계.md §4~6, 2채널로 축소 적용) ──
//   좌우 둘 다 검정(1,1) 2개 = 감속 마커 → 정지 마커.
//   CRUISE(baseSpeed) --감속마커--> APPROACH(approachSpeed) --정지마커--> 숏브레이크 정지.
//   정지 후 모터를 끄고 'g' 를 기다린다 — 그 사이 자로 x·y·θ 를 측정한다.
//
// 배선: + → ESP32 3V3, GND → ESP32 GND(로직 GND 레일), OUT → GPIO (아래 핀 참조)
// 극성: 검정에서 HIGH (기존 5채널과 동일 가정 — 실측으로 재확인할 것).

#include <WiFi.h>
#include <ArduinoOTA.h>

const char* WIFI_SSID = "여기에-AP-SSID";
const char* WIFI_PW   = "여기에-AP-비밀번호";  // 🔴 공개 저장소라 실제 값을 적지 않는다. 업로드 전에 여기만 채울 것.

// ── 핀 (README 기준 — 모터/STBY는 기존과 동일, 라인센서만 2채널로 교체) ──
#define PIN_PWMA   25
#define PIN_AIN1   26
#define PIN_AIN2   27
#define PIN_PWMB   14
#define PIN_BIN1   16
#define PIN_BIN2   17
#define PIN_STBY    4
#define PIN_LINE_L 13   // 기존 S1 자리 재사용
#define PIN_LINE_R 32   // 기존 S5 자리 재사용
const bool LINE_ACTIVE_LOW = false;   // 검정에서 HIGH — 실측으로 재확인할 것

const int PWM_FREQ = 20000, PWM_BITS = 8, PWM_MAX = 255;

// ── 조향 — 연속 PD 가 아니라 2상태 온-오프 보정 ──────────────
int turnDelta    = 40;    // 한쪽만 감지됐을 때 좌우 듀티 차이. 🔲 트랙에서 튜닝
int baseSpeed     = 120;  // CRUISE 기본 듀티
int approachSpeed = 70;   // APPROACH 감속 듀티 — 🔲 실측 튜닝 대상
const int CONTROL_MS = 20;

// ── 마커 검출 — "둘 다 검정" 이 5채널의 "5개 전부" 를 대체 ────
enum Phase { PH_CRUISE, PH_APPROACH };
Phase phase = PH_CRUISE;
int   stopIndex   = 0;
int   blackStreak = 0;
bool  markerLatch = false;
unsigned long lastMarkerMs = 0;
const unsigned long MARKER_GUARD_MS = 1000;
const int SHORT_BRAKE_MS = 150;

// ── 상태 ─────────────────────────────────────────────────
bool  motorsEnabled = false;
bool  pidRunning    = false;
bool  useRealSensor = true;    // 기본을 실측 모드로 (2026-08-21)
bool  simL = false, simR = false;   // 가상 모드 좌/우 감지 상태
unsigned long lastCtrlMs = 0, lastTelemMs = 0;

void setMotor(int in1, int in2, int pwmPin, int duty) {
  if (duty >= 0) { digitalWrite(in1, HIGH); digitalWrite(in2, LOW); }
  else           { digitalWrite(in1, LOW);  digitalWrite(in2, HIGH); duty = -duty; }
  ledcWrite(pwmPin, min(duty, PWM_MAX));
}

int dutyL = 0, dutyR = 0;
void applyDrive(int l, int r) {
  dutyL = l; dutyR = r;
  setMotor(PIN_AIN1, PIN_AIN2, PIN_PWMA, l);
  setMotor(PIN_BIN1, PIN_BIN2, PIN_PWMB, r);
}

void stopMotors() {
  applyDrive(0, 0);
  pidRunning = false;
  phase = PH_CRUISE;
  blackStreak = 0; markerLatch = false;
}

void doStop() {
  digitalWrite(PIN_AIN1, HIGH); digitalWrite(PIN_AIN2, HIGH);
  digitalWrite(PIN_BIN1, HIGH); digitalWrite(PIN_BIN2, HIGH);
  ledcWrite(PIN_PWMA, PWM_MAX);
  ledcWrite(PIN_PWMB, PWM_MAX);
  delay(SHORT_BRAKE_MS);
  applyDrive(0, 0);
}

void setEnabled(bool on) {
  motorsEnabled = on;
  digitalWrite(PIN_STBY, on ? HIGH : LOW);
  if (!on) stopMotors();
}

bool readL() {
  if (!useRealSensor) return simL;
  int v = digitalRead(PIN_LINE_L);
  return LINE_ACTIVE_LOW ? (v == LOW) : (v == HIGH);
}
bool readR() {
  if (!useRealSensor) return simR;
  int v = digitalRead(PIN_LINE_R);
  return LINE_ACTIVE_LOW ? (v == LOW) : (v == HIGH);
}

// 감속 마커 → APPROACH 진입 / 정지 마커 → 숏브레이크 정지
void onMarker() {
  if (phase == PH_CRUISE) {
    phase = PH_APPROACH;
    Serial.printf(">>> 감속 마커 감지 — APPROACH 진입 (속도 %d)\n", approachSpeed);
    return;
  }
  doStop();
  stopIndex = (stopIndex % 4) + 1;
  pidRunning = false;
  phase = PH_CRUISE;
  blackStreak = 0; markerLatch = false;
  Serial.printf(">>> 정지 마커 감지 — stopIndex=%d 도달. 정지 완료.\n", stopIndex);
  Serial.println(F("    자·모눈종이로 x/y/theta 측정 후 'g' 로 재출발할 것."));
}

// 좌우 둘 다 검정 2주기 연속 + 가드타이머 — 5채널 "5개 전부" 조건의 2채널판
void checkMarker() {
  if (!useRealSensor) return;
  bool allBlack = readL() && readR();
  if (allBlack) {
    blackStreak++;
  } else {
    blackStreak = 0;
    markerLatch = false;
  }
  if (blackStreak >= 2 && !markerLatch && (millis() - lastMarkerMs) > MARKER_GUARD_MS) {
    markerLatch = true;
    lastMarkerMs = millis();
    onMarker();
  }
}

void controlStep() {
  bool l = readL(), r = readR();
  int bs = (phase == PH_APPROACH) ? approachSpeed : baseSpeed;

  int corr = 0;
  if (l && !r)      corr = -turnDelta;   // 왼쪽만 감지 → 라인이 왼쪽 → 좌회전
  else if (!l && r) corr = +turnDelta;   // 오른쪽만 감지 → 우회전
  // (0,0) 중앙(또는 완전 이탈 — 구분 불가) / (1,1) 마커 통과 중 — 둘 다 직진 유지

  int lDuty = constrain(bs + corr, -PWM_MAX, PWM_MAX);
  int rDuty = constrain(bs - corr, -PWM_MAX, PWM_MAX);
  applyDrive(lDuty, rDuty);
}

void printHelp() {
  Serial.println(F(
    "\n── 2채널 조향 + 정지점 마커 시험 ─────────────\n"
    "  e : STBY 토글        g : 시작/재출발    s : 정지(수동, 마커 카운트 무관)\n"
    "  v : 가상/실측 센서 전환 (현재 기본: 실측)\n"
    "  [ : 가상 좌=1,우=0 (좌회전 상황)   ] : 가상 좌=0,우=1 (우회전 상황)\n"
    "  0 : 가상 좌=0,우=0 (중앙)          b : 가상 좌=1,우=1 (마커 테스트)\n"
    "  m : (실측 모드) 마커 강제 트리거\n"
    "  x : stopIndex 리셋 → 0\n"
    "  t / T : turnDelta -10 / +10\n"
    "  + / - : CRUISE 속도 ±20   a / A : APPROACH 속도 ±20\n"
    "  ? : 이 목록\n"
    "───────────────────────────────────────────────\n"
    "검증: '[' → 좌 듀티 감소·우 증가 (좌회전) 이면 정상\n"
    "정지산포 측정: 'v' 로 실측 전환 → 'g' 로 CRUISE 시작 → 정지 마커에서 자동 정지\n"
    "              → 자로 x/y/theta 측정 → 'g' 로 재출발, 정지점당 10회 반복\n"
    "⚠ 두 센서 다 흰 바닥일 때가 '정상 중앙'과 '완전 이탈'을 구분 못한다 — 알려진 한계."));
}

void setup() {
  Serial.begin(115200);
  delay(300);
  pinMode(PIN_STBY, OUTPUT);
  digitalWrite(PIN_STBY, LOW);
  pinMode(PIN_AIN1, OUTPUT); pinMode(PIN_AIN2, OUTPUT);
  pinMode(PIN_BIN1, OUTPUT); pinMode(PIN_BIN2, OUTPUT);
  pinMode(PIN_LINE_L, INPUT);
  pinMode(PIN_LINE_R, INPUT);
  ledcAttach(PIN_PWMA, PWM_FREQ, PWM_BITS);
  ledcAttach(PIN_PWMB, PWM_FREQ, PWM_BITS);
  stopMotors();

  WiFi.mode(WIFI_STA);
  WiFi.begin(WIFI_SSID, WIFI_PW);
  ArduinoOTA.setHostname("hazardbot-drive");
  ArduinoOTA.onStart([]() { setEnabled(false); Serial.println("\nOTA 수신 — 모터 차단"); });
  ArduinoOTA.begin();

  printHelp();
  Serial.println(F("⚠ 실측 모드다. 실제 센서를 바로 읽는다. 가상 모드로 방향만 확인하려면 'v'."));
}
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

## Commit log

2026-04-30 초기 커밋: HazardBot 2026 프로젝트 스켈레톤
    - 영문 폴더 구조(firmware/ros2_ws/hardware/docs)
    - ESP32 #1 펌웨어 v5(가스/화염 상태 판정 + XOR 체크섬 메시지)
    - README, .gitignore, 아키텍처 개요 문서
2026-04-30 feat: ESP32 #2 펌웨어 + STL 가이드 + CI + 협업 문서 추가
    - firmware/esp32_arm/esp32_arm.ino: STS3215 6축 제어 스켈레톤
    (FreeRTOS 듀얼 코어, 컴플라이언스 임계값, Wi-Fi TCP 골격)
    - hardware/stl/: SO-ARM101 다운로드 가이드 + sparse-checkout 스크립트
    (.gitignore에 *.stl 추가, custom/ 예외)
    - .github/workflows/arduino.yml: ESP32 펌웨어 컴파일 검증
    - .github/workflows/ros2.yml: ROS2 Jazzy colcon build/test (패키지 자동 감지)
    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
2026-04-30 docs: README를 Boogie 스타일로 재작성 + 미검증 STL 스크립트 삭제
    - README: 이모지 헤더, 참가정보, Architecture/Hardware 표,
    System Process · Source code · 추후 활용방안 details/summary 박스 추가
    - 팀원 실명 반영 (박승환 / 윤강희 / 이진우)
    - hardware/stl/download_stl.{sh,ps1} 삭제: SOURCE_PATH 미검증으로
    실행 시 잘못된 경로 시도 우려. README 수동 안내만 남김
    - hardware/stl/README: 자동 다운로드 섹션 제거
2026-04-30 hw: SO-ARM101 STL 3종 추가 (Base / Prusa / Ender)
    - hardware/stl/Base_SO101.stl (0.47 MB)
    - hardware/stl/Prusa_Follower_SO101.stl (4.83 MB)
    - hardware/stl/Ender_Follower_SO101.stl (24.82 MB)
    - LeRobot SO-ARM101 오픈소스 프레임. 사용 프린터에 맞춰 Prusa/Ender 중 선택
    - .gitignore: hardware/stl/ 하위 STL은 추적 대상으로 화이트리스트
    - .gitattributes 신규: STL/펌웨어 바이너리 binary 처리, 소스 LF 강제
    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
    [Base_SO101.stl, Prusa_Follower_SO101.stl]
2026-05-20 feat: 로컬 프로젝트 파일 추가 (코드, 계획, 참고 문헌, 구성품 목록)
    [HazardBot_v4_전체_구성품_목록.xlsx, HazardBot_기획학습단계_구성품목록.xlsx, SO-ARM101_3D Printing.xlsx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]
2026-05-20 refactor: 코드/ 폴더를 README 폴더 구조에 맞게 재정렬
    - 코드/Robot Arm/Arduino/arm_firmware/ → firmware/esp32_arm/arm_firmware/
    - 코드/Robot Arm/Arduino/set_servo_id.ino → firmware/esp32_arm/set_servo_id.ino
    - 코드/ROS2/vision_node/ → ros2_ws/src/vision_node/
    - 코드/AMR/ 삭제 (firmware/esp32_amr/esp32_amr.ino에 v5 내용 이미 존재)
    - firmware/esp32_arm/esp32_arm.ino 삭제 (단일 파일 스켈레톤 → 멀티파일 버전으로 대체)
    [hsv_calibration.yaml]
2026-05-20 chore: 소스코드 외 비개발 파일 삭제
    - 계획/ 삭제 (기획 문서 .docx, .xlsx)
    - 참고 문헌/ 삭제 (논문 PDF)
    - HazardBot_v4_전체_구성품_목록.xlsx 삭제
    [HazardBot_v4_전체_구성품_목록.xlsx, HazardBot_기획학습단계_구성품목록.xlsx, SO-ARM101_3D Printing.xlsx]
2026-05-20 docs: README 불필요 섹션 제거 및 경로 수정
    - 추후 활용방안 섹션 삭제 (발표용 홍보 문구)
    - 팀/일정 섹션 삭제 (contributing.md에 중복, 일정 낡음)
    - Mission FSM, Sensor Fusion 섹션 삭제 (미구현 예정 항목)
    - 마지막 인사말 삭제
    - ARM 펌웨어 경로 수정: esp32_arm/esp32_arm.ino → esp32_arm/arm_firmware/arm_firmware.ino
    - Vision Pipeline 경로 수정: hazardbot_vision/ (예정) → vision_node/
    - 폴더 구조 섹션을 실제 구조에 맞게 업데이트
2026-05-20 chore: firmware 하위 README 파일 삭제
2026-06-01 docs: HazardBot 계획변경·개선안 v5 — 마스터 정본 [W1 · 06/01]
2026-06-04 chore: 저장소 구조 정비 — .gitignore 확장 · 구 팔 펌웨어 아카이브 이관 [W1 · 06/04]
2026-06-07 feat: amr_bridge/arm_bridge TCP 브릿지 초기 구현
    RPi5를 TCP 서버로, 양쪽 ESP32를 클라이언트로 하는 통신 구조.
    <CMD,값1,...,체크섬> 프로토콜 표준화 (체크섬=ASCII합%256).
    amr_bridge: 포트5000, SENS/GAS/TEMP/BATT 수신, MOVE/STOP 송신
    arm_bridge: 포트5001, SFBACK 수신, ARM/LED/BUZZ 송신
2026-06-08 docs(arm): 로봇암 초기 계획 — LeRobot 0.4.4 환경 구축 [W2 · 06/08]
2026-06-11 feat: hazard_detector·arm_controller(IK)·mission_orchestrator·대시보드 초기 구현
    - hazard_detector: 구역별 임계값 차등, MQ비율 분석, 화염 즉시 L3
    - arm_controller: 기하학적 IK(코사인법칙) + 포즈테이블 + 관절한계검증
    - mission_orchestrator: FSM (IDLE~REPORT/EMERGENCY), 양쪽ESP32 동시 STOP
    - hazardbot_dashboard: Flask+SocketIO 실시간 웹 모니터링, launch 파일 포함
2026-06-15 feat(firmware): STS3215 버스 점검 스케치 [W3 · 06/15]
2026-06-18 feat: vision_node 초기 구현 (HSV + minAreaRect)
    cv2.VideoCapture(0) 직접 오픈 방식.
    색상 마스크 -> 컨투어 -> minAreaRect로 중심/크기/방위각 추출.
    종횡비 기반 형태 판정 포함.
2026-06-20 feat(firmware): 리더 서보 ID 부여 스케치 — 끝단→베이스 순서 [W3 · 06/20]
2026-06-22 feat(hardware): SO-ARM101 섀시 어댑터 베이스 v1 [W4 · 06/22]
    [Base_SO101.step, Base_SO101_chassis_v1.step, Base_SO101_chassis_v1.stl]
2026-06-23 feat(hardware): 섀시 어댑터 베이스 v2 개정 [W4 · 06/23]
    [Base_SO101_chassis_v2.step, Base_SO101_chassis_v2.stl]
2026-06-24 feat(hardware): TB3 카메라 프레임 · PCB 서포트 STEP [W4 · 06/24]
    [tb3_pcb_support-ibb-01.stp, tb3_pi_camera_frame.stp]
2026-06-25 feat(hardware): Waffle 플레이트 3mf · Hexagon Case [W4 · 06/25]
    [Hexagon Case.stl, Waffle_Plate.3mf]
2026-06-26 feat(hardware): 카메라 프레임 슬라이싱 · PLA 출력 [W4 · 06/26]
2026-06-27 feat(arm): 리더 가동범위 실측 도구 [W4 · 06/27]
2026-06-28 feat(arm): 리더 캘리브레이션 1차 — 캘리브·ID·점검 도구 [W4 · 06/28]
2026-06-28 fix: vision_node/dashboard를 camera_ros 토픽 구독 방식으로 전환
    원인: ros-jazzy-libcamera 구버전 소스가 미디어 엔티티 이름을 하이픈으로
    하드코딩, 실제 커널 드라이버는 언더스코어 사용 -> CFE acquire 항상 실패.
    GitHub 최신 libcamera 소스 직접 빌드 + LD_PRELOAD로 우회, camera_ros가
    /camera/image_raw 30fps 안정 스트리밍 확인.
    camera_ros가 카메라를 점유하므로 vision_node/dashboard의
    cv2.VideoCapture(0) 직접 오픈 방식 제거 -> cv_bridge로 토픽 구독.
    vision_node 작업 중 만난 의존성 문제 3건 해결 (상세: vision_node/DEPENDENCY_NOTES.md):
    - cv_bridge 시스템 미설치 -> ros-jazzy-cv-b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
    [vision_node.py]
2026-06-29 feat(arm): 엔코더 래핑 대응 — 버스·목표위치·모니터 도구 [W5 · 06/29]
